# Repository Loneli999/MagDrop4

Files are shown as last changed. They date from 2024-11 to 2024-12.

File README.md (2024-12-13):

# MagDrop4
MagDrop4 is an interactive Connect4-playing machine designed to compete against a human player in real-time. The machine uses a custom-built linear belt actuator with an electromagnet to pick up magnetic game pieces from a magazine, move to the chosen column, and release each piece with accuracy. Sensors at each column track the human player's moves, allowing MagDrop4 to respond strategically, adapting its decisions based on the game’s progression. MagDrop4 showcases embedded system principles, combining real-time sensor feedback, mechanical actuation, and game strategy for an engaging human-machine interaction.

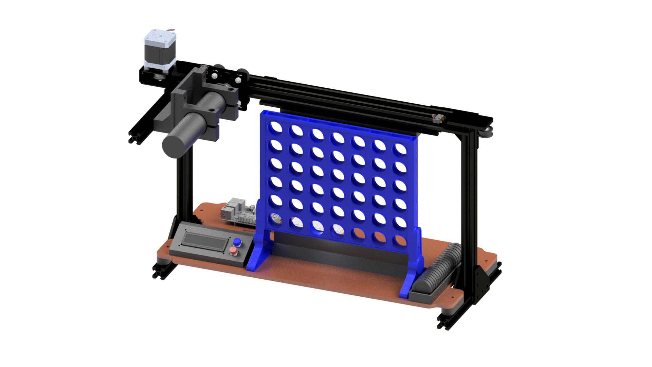
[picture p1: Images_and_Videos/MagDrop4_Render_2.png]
MagDrop4


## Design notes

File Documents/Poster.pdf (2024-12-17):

MagDrop4 | EECS 149/249A - 2018
| Leon Greiner, Murtaza Yar Hiraj, Giorgiana Rosas, Ashvin Verma
Projective Goal MagDrop4 is a real-time, interactive Connect4-playing machine designed to compete against a human on a physical Connect4 board. It uses IR sensors to detect human moves, a game AI to calculate optimal responses, and an electromagnet with magnetic game pieces for precise handling and placement. A custom belt driven linear actuator, powered by a stepper motor, ensures accurate piece placement. This project showcases advanced sensor integration, motor control, and AI-driven | | Game Engine The game engine uses a Minimax algorithm enhanced with Alpha-Beta Pruning to optimize the AI's moves efficiently. A heuristic evaluates board states by scoring windows with 4, 3, and 2 AI pieces as (+100, +10, +5), penalizing opponent windows as (-100, -8, 0), and prioritizing central play.

decision-making in a dynamic autonomous system.

## Mechanical Design

The main structure is built from standard aluminum profiles, which also serve as the guide rail for the gantry cart of the linear actuator. The baseplate is precision laser-cut from plywood. Numerous components, including mountings, the magazine, and game discs, are 3D-printed using PLA. The magazine uses a spring mechanism to continuously push the game discs toward the grabbing point..

## System Integration and Results

The final system delivers real-time interaction, accurate gameplay execution, and competitive AI performance, showcasing the success of combining precision mechanics, sensor integration, and advanced algorithms. The gantry cart completes its cycle in <5 secs: detecting human play, computing the AI’s move, placing a piece, and resetting for the next turn. This highlights the system’s speed and seamless integration.

2024

## Machine Logic

The system uses a Finite State Machine (FSM) to manage gameplay flow: It detects human moves via IR
sensors, calculates the AI’s optimal move using the game
engine, and precisely places pieces with the belt driven
linear actuator. | Electrical Design
| The electrical system is built around a Raspberry Pi 3+,
| handling motor control, sensor inputs, and display output. Power is supplied via 5V and 16V lines, with an I2C interface
| managing the display and the stepper motor controlled by a
| DRV8825 motor driver, connected via an extension board to
| the Raspberry. Furthermore, we use an N-channel logic-level
| MOSFET to control the 16V electromagnet via a GPIO pin.

Simplified illustration of the Systems FSM

Disc Magazine

Gantry Cart with
Electromagnet

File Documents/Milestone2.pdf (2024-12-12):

# Project Title: MagDrop4

Team: Leon Greiner, Murtaza Yar Hiraj, Giorgiana Rosas, Ashvin Verma

EECS 149/249A Milestone 2, Fall 2024

## Project Goal

The goal of MagDrop4 is to create an engaging and competitive Connect4-playing machine that can seam-lessly interact with a human player in real-time. By integrating advanced embedded systems, mechanical precision, and strategic gameplay, MagDrop4 aims to demonstrate the capabilities of autonomous systems in responsive, interactive applications. The project also serves as a practical exploration of sensor integration, motor control, and real-time decision-making within an embedded system framework.

## Progress

Mechanical Design

We have completed printing all the 3D parts and assembling the mechanical structure of the machine. The mechanical structure mainly consists out of normed aluminum profiles, which can be easily assembled. The final step remaining is to create the baseplate. We are currently deciding whether to laser-cut the plate or manually cut and drill it from plywood, depending on the availability of a laser cutter.

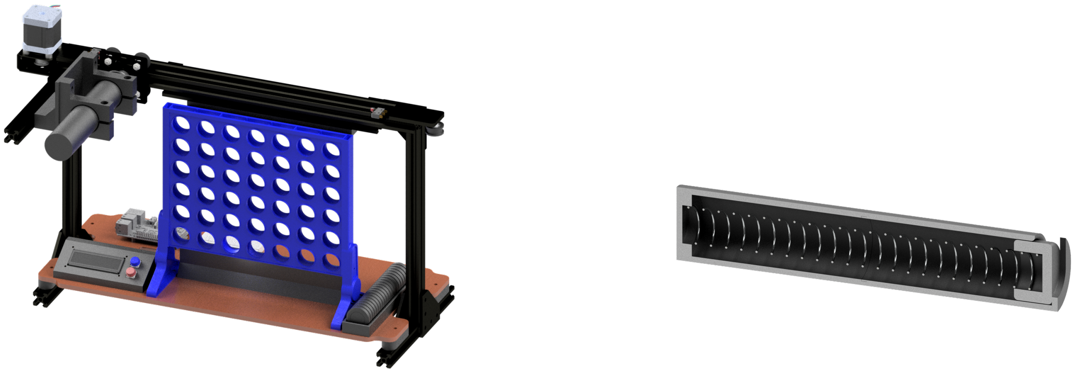
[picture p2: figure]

Figure 1: CAD Rendering of MagDrop4

Figure 2: CAD Rendering of the Game Piece Magazine

Electrical Design

The electrical design includes the complete circuitry, with the Raspberry Pi serving as the central control unit. The display is managed via an SPI interface, utilizing GPIO pins 10, 9, 8, and 7. A stepper motor is driven by the DRV8829 driver, conveniently connected through a extension shield. The motor control uses GPIO 11 for direction, GPIO 12 (PWM) for step control, and GPIO 13 for enable. The Motor gets powered by a 24V. For the human move detection, seven IR sensors are powered by 5V. These sensors provide a simple high/low signal depending on whether a move is detected, and they are connected to GPIO pins 0 through 6. Each sensor’s sensitivity can be adjusted individually using a sensitivity screw on the sensor. Two limit switches are used to mark the farthest left and right positions of the gantry cart on the linear rail. These are configured in a Normally Open (NO) setup, connected to GPIO pins 14 and 15. Each switch is connected to 3.3V through a pull-up resistor. Similarly, two additional buttons for user input are connected to GPIO pins 16 and 17 in the same NO configuration.

FSM and Machine Logic

The following FSM diagram illustrates the complete logic of the machine, starting from the initial setup to the conclusion of the game, either when there is a winner or the game ends in a draw. At the beginning, the machine moves the gantry cart away from the magazine, so there is more room to reload the magazine with the game pieces. Then the machine prompts the user to confirm if the magazine is fully loaded with game pieces and whether the game can proceed. Before starting, the user is also given the opportunity to adjust the AI’s difficulty level. During Human Turn, the system checks if the IR sensor for a specific column is triggered and after that the machine waits for up to 2 seconds for a valid new IR trigger. This allows for situations where the human player initially places a piece in one column, but then decides to retrieve it and drop it into another. The Game Engine, which handles the rules and logic for determining the next moves and checking for game completion, will be detailed in a separate section. The AI Turn controls the movement of the gantry cart to the desired column and manages the activation and deactivation of the electromagnet to place the game piece accurately.

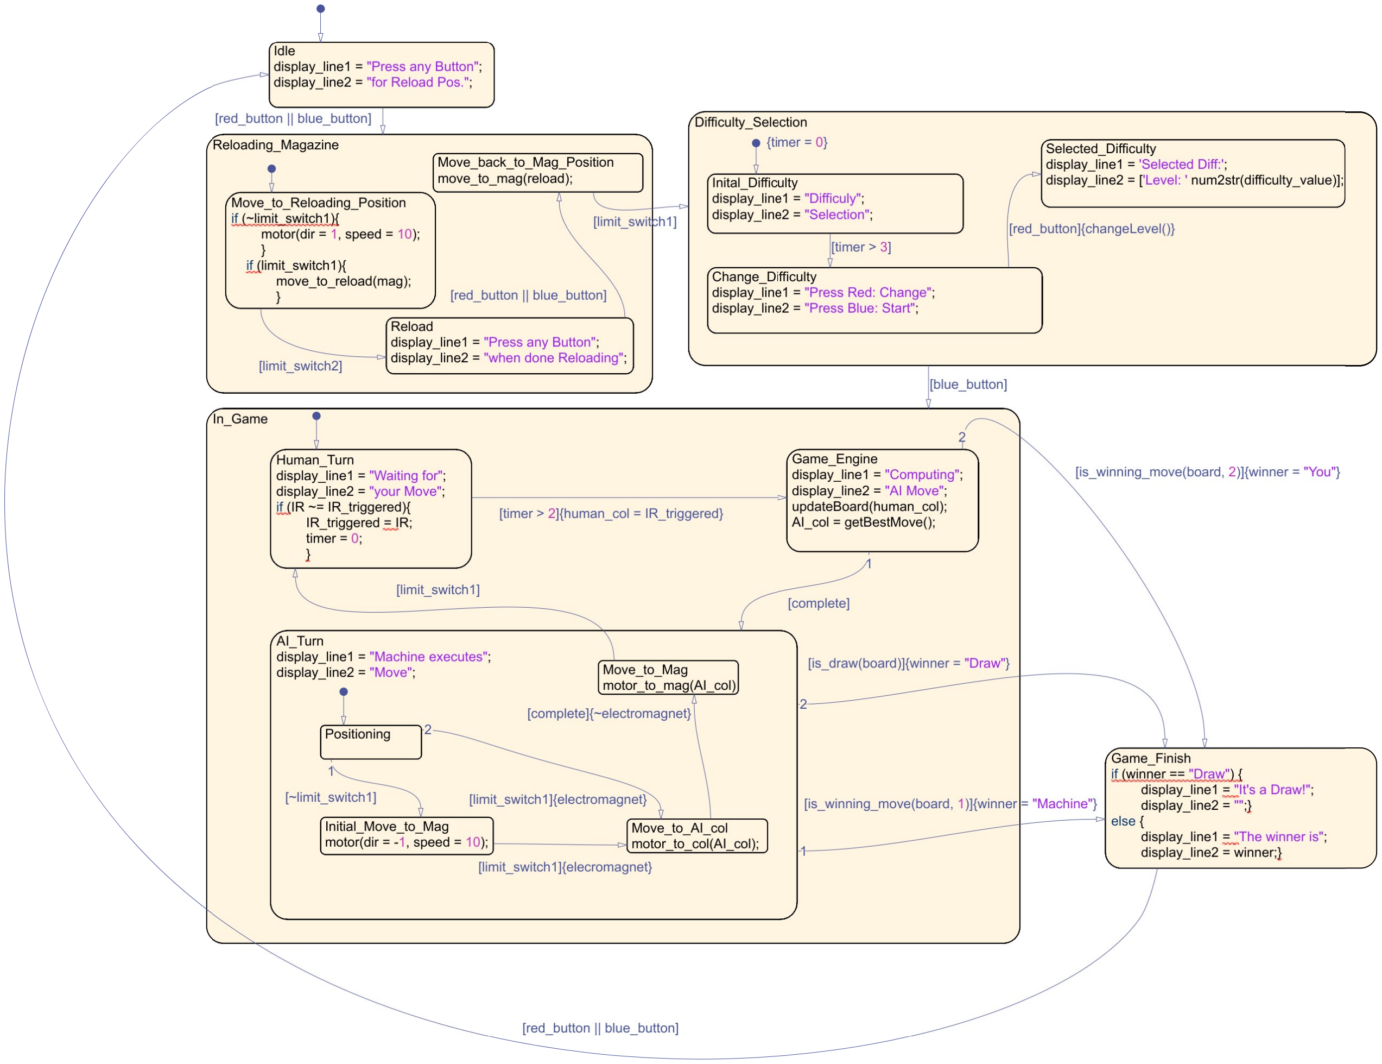
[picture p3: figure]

Figure 3: Finite State Machine of MagDrop4

Game Engine

We successfully developed a functional game engine prototype, which computes the computer’s move in maximum 30 ms (depth = 4) on a standard laptop. This suggests it should operate within acceptable time limits on the Raspberry Pi 3+. The game engine utilizes a Minimax Search algorithm with Alpha-Beta Pruning, allowing us to implement different difficulty levels by adjusting the search depth (ranging from 1 to 4).
Minimax is a tree search algorithm that evaluates all possible moves by both the human and the computer up to a specified depth. At the terminal nodes of the tree, a scoring function determines the relative value of the board position. The scoring system is critical for the game engine’s effectiveness. We have chosen the following scoring parameters, which can be fine-tuned as needed:
- AI’s 3-in-a-Row with 1 Empty Space: score + = 10
- AI’s 2-in-a-Row with 2 Empty Spaces: score + = 5
- Human 3-in-a-Row with 1 Empty Space: score − = 15
- Terminal State (AI Wins): score + = 100, 000
- Terminal State (Human Wins): score − = 100, 000

We also included Alpha-Beta Pruning, which enhances computational efficiency by eliminating branches in the search tree that cannot influence the final outcome. This significantly reduces the number of paths evaluated and speeds up decision-making. At a search depth of 4, the AI is already challenging to beat and sufficient for our purposes. Increasing the depth to 6 makes it basically impossible for a human to win against the machine. However, the computational cost increases exponentially, potentially exceeding the capabilities of the Raspberry Pi 3+. Further testing is required to determine the feasibility of deeper searches on the hardware.

## Resources

Name | Quantity | Name | Quantity
400-Point Breadboard | 1 | M3 Screw | 17
Aluminum Spacer | 4 | M5 Nut | 25
Belt Clamp | 2 | M5 Screw | 100
Connect 4 Game Set | 1 | M5 T-Nut | 1
Corner Connector 2020 | 1 | Metal Disk Inserts | 42
Display | 1 | Limit Switch Plate | 2
DRV8825 Extension Board | 1 | Mosfet | 1
Electromagnet | 1 | Raspberry Pi 3 Model B+ | 1
Gantry Cart | 1 | Round Switch | 2
GT2 Belt | 1 | Spring | 1
Idler Pulley | 1 | Stepper Motor | 1
Idler Pulley Plate | 1 | Stepper Motor Driver (DRV8825) | 1
IR Sensor | 7 | Superglue | 1
L-Connector | 7 | Timing Pulley | 1
Limit Switch | 2 | USB 2.0 A to Micro B cable | 1
M2.5 Screw | 4 | USB Power Supply | 1
M3 Insert x 5mm | 7 | V-Slot 20x20 100mm | 4
V-Slot 20x20 200mm | 1 | V-Slot 20x20 300mm | 3
V-Slot 20x40 500mm | 1 | V-Slot Cover | 2
V-Slot Endcap | 2
3D Printed Parts
Base Plate Spacer | 4 | Disk Holder | 1
Control Mount | 1 | Idler Pulley Overlay | 1
Disk | 42 | IR Mount Plate | 1
Disk Barrier | 1 | Raspberry Pi Standoff | 4
Spring Top | 1 | Base Plate (Laser Cut) | 1

Table 1: Purchase and Checkoff Parts List with Additional 3D Printed Parts

## Timeline

- 12.10. - Completion of Wiring: All electrical components, including sensors, motors, and actuators, are fully wired and tested for connectivity.
- 12.14. - Code Implementation Finalized: Core logic for gameplay, motor control, and sensor integration are implemented.
- 12.16. - Bug Fixing and Full Machine Operation: Final debugging and calibration completed. The machine is fully functional and ready for demonstration.

## GitHub Repo

https://github.com/Loneli999/MagDrop4.git

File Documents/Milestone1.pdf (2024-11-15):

# Project Title: MagDrop4

Team: Leon Greiner, Murtaza Yar Hiraj, Giorgiana Rosas, Ashvin Verma

EECS 149/249A Milestone 1, Fall 2024

## Project Goal

The goal of MagDrop4 is to create an engaging and competitive Connect4-playing machine that can seamlessly interact with a human player in real-time. By integrating advanced embedded systems, mechanical precision, and strategic gameplay, MagDrop4 aims to demonstrate the capabilities of autonomous systems in responsive, interactive applications. The project also serves as a practical exploration of sensor integration, motor control, and real-time decision-making within an embedded system framework.

## Project Approach

To achieve this, MagDrop4 combines a custom-built linear belt actuator, powered by a stepper motor, with an electromagnet end effector that precisely handles and places the custom-made 3D printed game disks with steel inserts. A set of IR sensors at each column allows the machine to monitor and react to the human player’s moves, updating its strategy based on the evolving game state. The system is powered by a Raspberry Pi, which manages the game logic, motor control, and sensor input, creating a dynamic response to each move.

## Progress

We’ve developed a first prototype of MagDrop4 in CAD (see Figure 1). We successfully designed a beltdriven system powered by a single stepper motor. This stepper motor with a step size of 0.9°, combined with two limit switches positioned at the ends of the rail, ensures precise movement of the sledge. While this prototype is a great initial step, several improvements are planned. We need to redesign the magazine to increase its capacity, allowing for more game pieces to be stored and deployed. Additionally, we still need to implement the mounting for the linear sled, as it currently hovers without a fixed support structure.

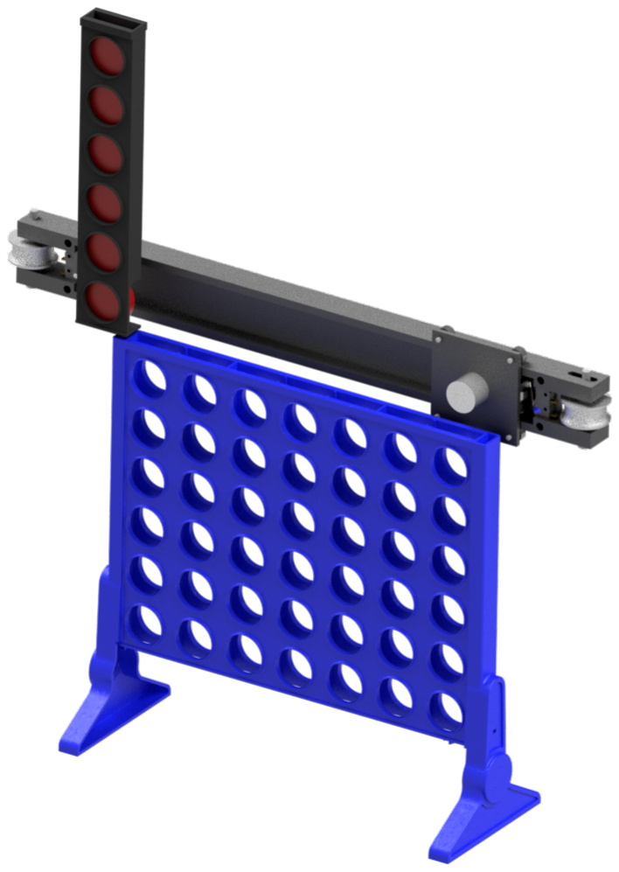
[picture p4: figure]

Figure 1: Rendering of the first prototype

1

## Resources

All the essential parts for MagDrop4 are listed in the table, showing both items we’re purchasing and those we already have on hand, each with its corresponding price and checkoff number. We’ve slightly exceeded the $100 budget, but this covers all important components, including a Raspberry Pi, a stepper motor, power supplies, and bearings.
Our custom frame components, including the rail, sled, and mounting structures will be 3D printed. This approach gives us flexibility in the design process and is virtually free, since we can use the 3D printers in Cory Supernode and pay for the filament we use. Besides these listed items, only minor additions like wires or washers may be needed as we assemble the system.
Name | Qty | Checkoff # | Price | Link
Raspberry Pi 3 Model B+ | 1 | 13 | - | Link (https://www.raspberrypi.com/products/raspberry-pi-3-model-b-plus/)
Electromagnet | 1 | 245 | - | Link (https://www.amazon.com/uxcell-Electric-Lifting-Electromagnet-Solenoid/dp/B01N3387AA)
Limit Switch | 2 | 145 | - | Link (https://www.amazon.com/InduSKY-Switch-Momentary-Roller-Switches/dp/B08736NP44)
IR Receiver & Transmitter | 7 | 265 | - | Link (https://www.amazon.com/Digital-Receiver-Transmitter-Electronic-Building/dp/B08X2MFS6S)
Stepper Motor | 1 | 213 | - | Link (https://www.ebay.com/itm/154024578430)
On-Off Toggle Switch | 1 | 141 | - | Link (https://www.amazon.com/Position-Automobile-Appliance-Industrial-Control/dp/B07XB2JC14)
USB Power Supply | 1 | 301 | - | Link (https://thereviewindex.com/us/p/Wall_Charger_UROPHYLLA_3_Pack_5V_2_4A_Mini_Universal_Portable_Home_Travel_Adapter_USB_Wall_Charger_f/AZ-US_B06X9PY6RT)
USB 2.0 A to Micro B cable | 1 | 318 | - | Link (https://thereviewindex.com/us/p/Wall_Charger_UROPHYLLA_3_Pack_5V_2_4A_Mini_Universal_Portable_Home_Travel_Adapter_USB_Wall_Charger_f/AZ-US_B06X9PY6RT)
Connect 4 Game Set | 1 | - | $ 9.99 | Link (https://www.amazon.com/Hasbro-A5640-Connect-4-Game/dp/B00D8STBHY)
Sledge Bearing (BS69310-5) | 6 | - | $ 10.20 | Link (https://www.aliexpress.us/item/1005003690085583.html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)
Stepper Motor Driver (DRV8825) | 1 | - | $ 8.99 | Link (https://www.amazon.com/DiGiYes-DRV8825-Stepper-Driver-Printer/dp/B0BXL5VYPT)
DRV8825 Extension Board | 1 | - | $ 7.99 | Link (https://www.amazon.com/Ximimark-DRV8825-Printer-Stepper-Extension/dp/B07L74WZPS)
Power Supply 24V | 1 | - | $ 19.99 | Link (https://www.amazon.com/EMITEVER-Lighting-Transformers-100-240V-UL-Listed/dp/B095VWHPCC?s=hi)
Timing Pulley with Teeth (2GT-40T 11 5) | 1 | - | $ 5.35 | Link (https://www.ebay.com/itm/156393844989?_skw=2gt+40t&itmmeta=01JC6F1FEDNC6WNQF3JPT0Q8V1&var=457485017278)
Timing Pulley without Teeth (2GT-40T 11 5) | 1 | - | $ 5.35 | Link (https://www.ebay.com/itm/226059144256)
2GT Timing Belt | 1 | - | $ 2.95 | Link (https://www.ebay.com/itm/256243562695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)
Steel Disk Inserts | 1 | - | $ 19.99 | Link (https://www.amazon.com/totalElement-Steel-Discs-Strike-Plates/dp/B09BXWJ772?sp_csd=d2lkZ2V0TmFtZT1zcF9hdGY)
Various Screws, Nuts and Washers | 1 | - | ≈ $ 30 | Link (https://www.ebay.com/itm/256243562695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)
Total | | | $120.81

Table 1: Purchase and Checkoff Part List

## Major Risks

Major risks include challenges in constructing and testing the custom linear actuator, ensuring smooth integration of hardware and software components, and maintaining real-time response accuracy to enable interactive gameplay. Additionally, reliance on 3D-printed parts introduces potential delays or issues with part quality, which could impact system precision and reliability.

## Timeline & Responsibilities

- November 18: Murtaz and Giorgiana finish the game software model
- November 21: Leon and Ashvin finalize actuator assembly and testing.
- November 28: Finish hardware and software integration
- December 8: Work on final demo and integration

## GitHub Repo

https://github.com/Loneli999/MagDrop4.git

2

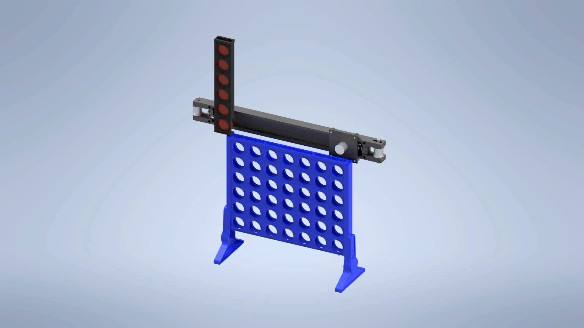
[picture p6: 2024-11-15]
Images_and_Videos/Render_Animation_Prototype_1.gif

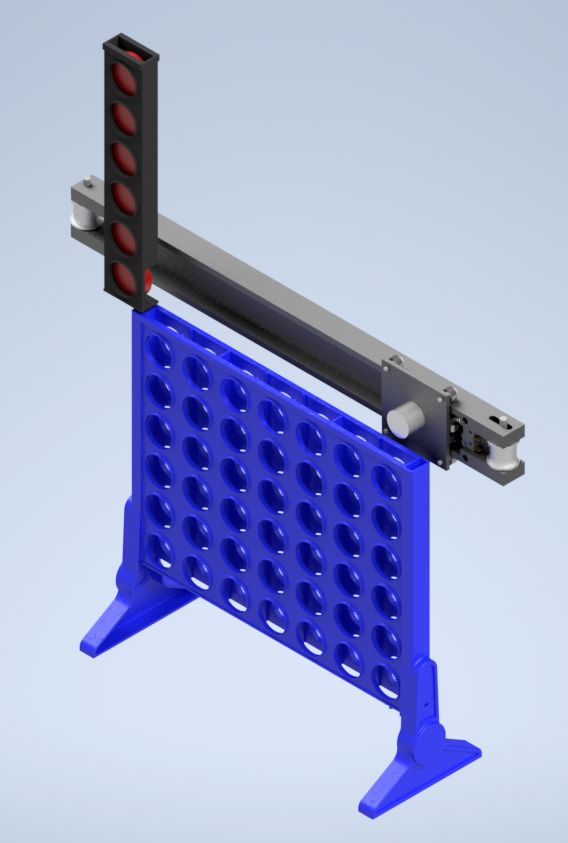
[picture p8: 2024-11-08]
Images_and_Videos/Render_Prototype_1_cropped.png

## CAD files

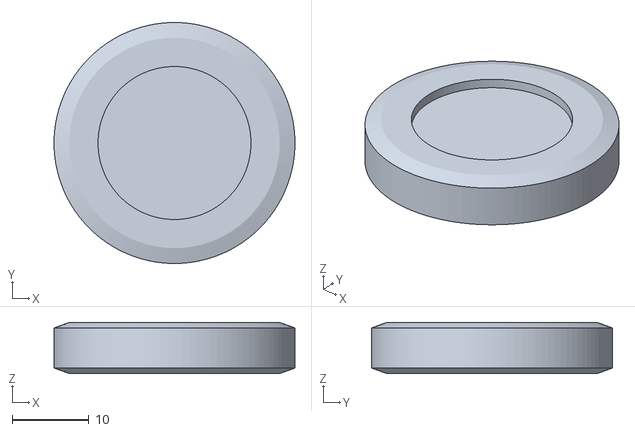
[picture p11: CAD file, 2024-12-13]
CAD_Model/3DPrint_Parts/3DPrint_Files/Disk_machine.stl
31.5 x 31.5 x 6.70

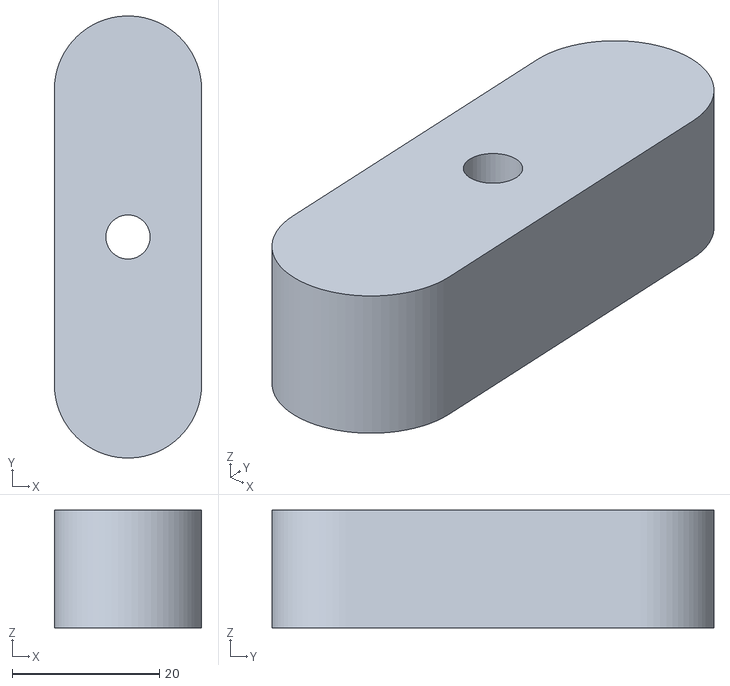
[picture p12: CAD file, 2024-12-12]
CAD_Model/3DPrint_Parts/3DPrint_Files/Base_Plate_Spacer.stl
20.0 x 60.0 x 16.0

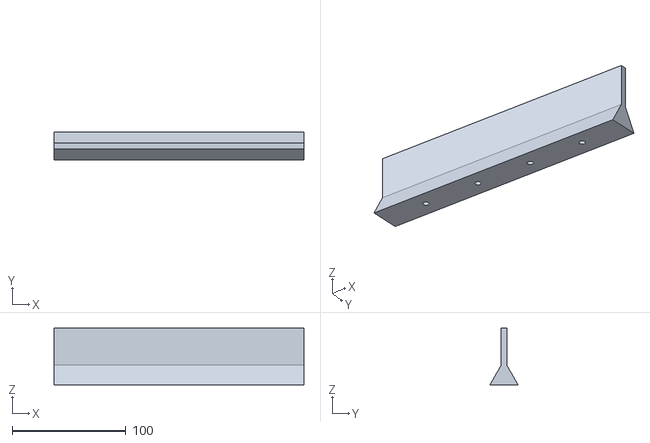
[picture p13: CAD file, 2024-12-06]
CAD_Model/3DPrint_Parts/3DPrint_Files/Disk_Barrier.stl
220.0 x 25.0 x 50.0

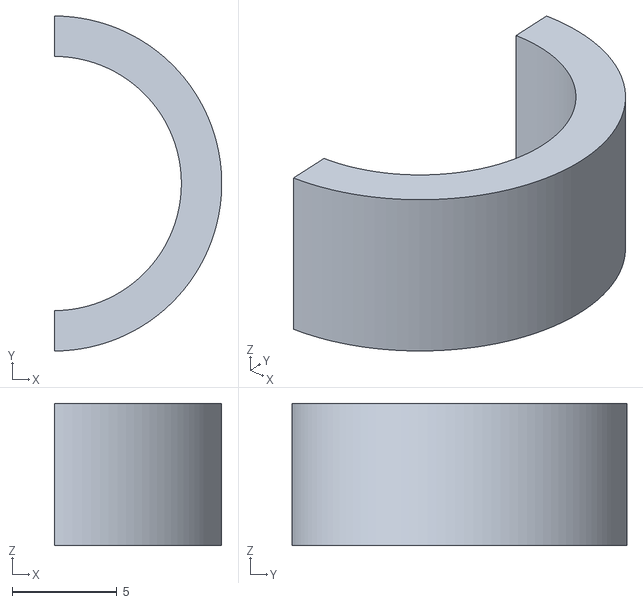
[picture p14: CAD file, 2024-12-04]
CAD_Model/3DPrint_Parts/3DPrint_Files/Idler_Pulley_Insert.stl
8.00 x 16.0 x 6.80

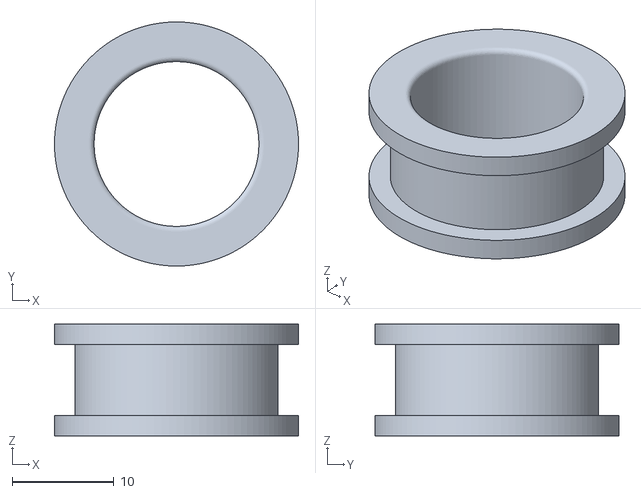
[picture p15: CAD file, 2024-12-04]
CAD_Model/3DPrint_Parts/3DPrint_Files/Idler_Pulley_Overlay.stl
24.0 x 24.0 x 11.0

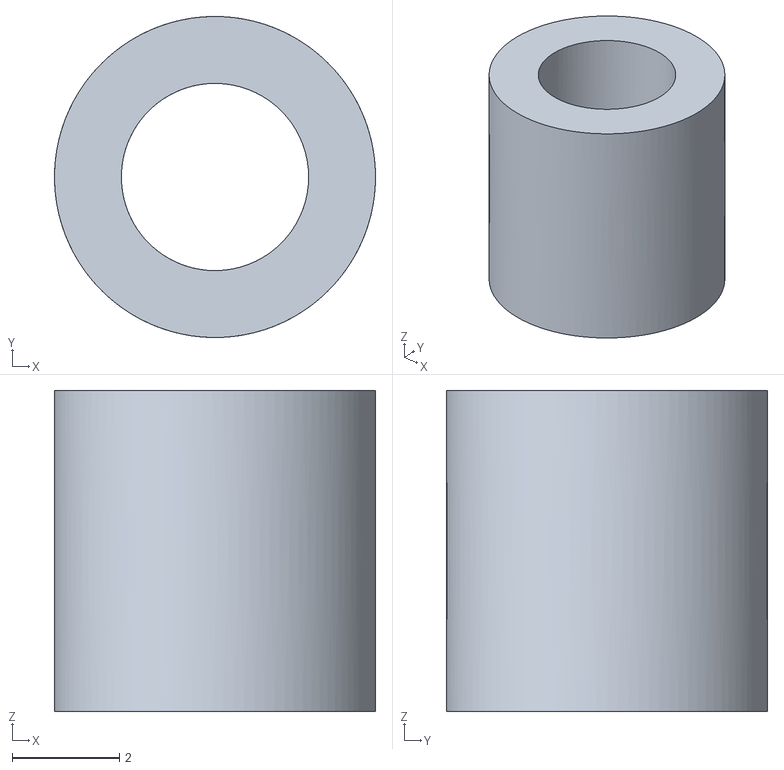
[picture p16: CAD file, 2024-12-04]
CAD_Model/3DPrint_Parts/3DPrint_Files/Raspberry_Pi3_Standoff.stl
6.00 x 6.00 x 6.00

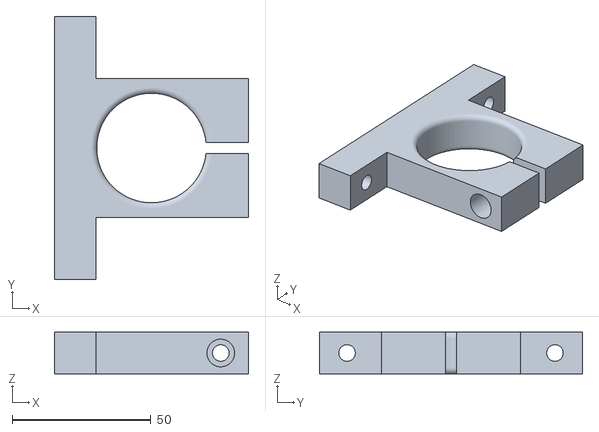
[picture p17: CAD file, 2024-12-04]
CAD_Model/3DPrint_Parts/3DPrint_Files/Magazine_Holder.stl
70.0 x 95.0 x 15.0

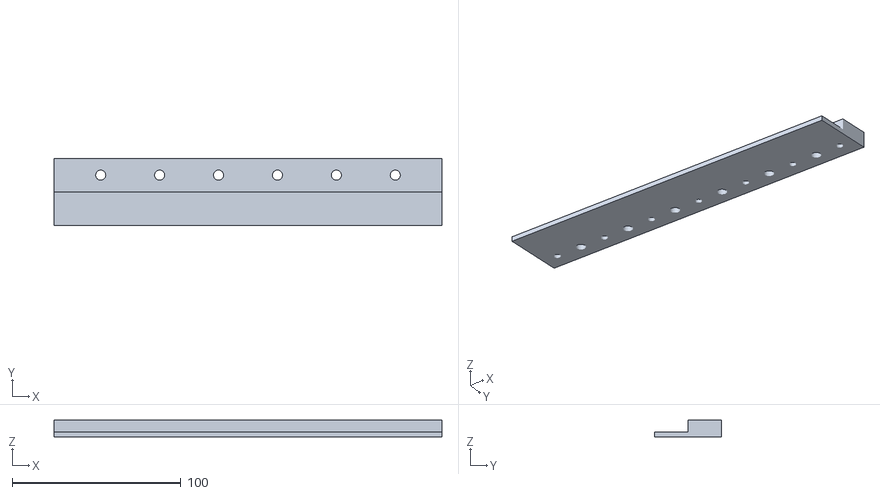
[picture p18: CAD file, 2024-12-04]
CAD_Model/3DPrint_Parts/3DPrint_Files/IR_Mount_Plate.stl
230.0 x 40.0 x 10.0

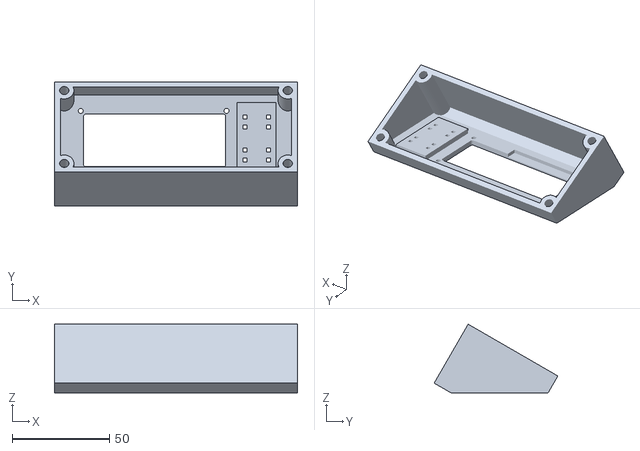
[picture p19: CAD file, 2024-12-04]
CAD_Model/3DPrint_Parts/3DPrint_Files/Control_Mount.stl
125.0 x 63.7 x 35.3

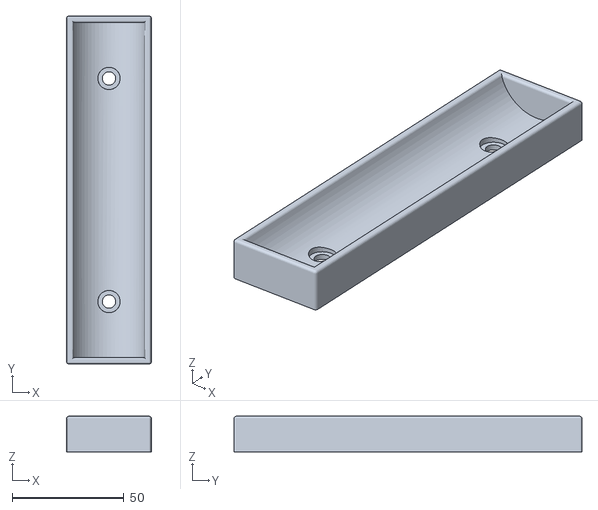
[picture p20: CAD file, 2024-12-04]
CAD_Model/3DPrint_Parts/3DPrint_Files/Disk_Holder.stl
38.0 x 156.0 x 16.0

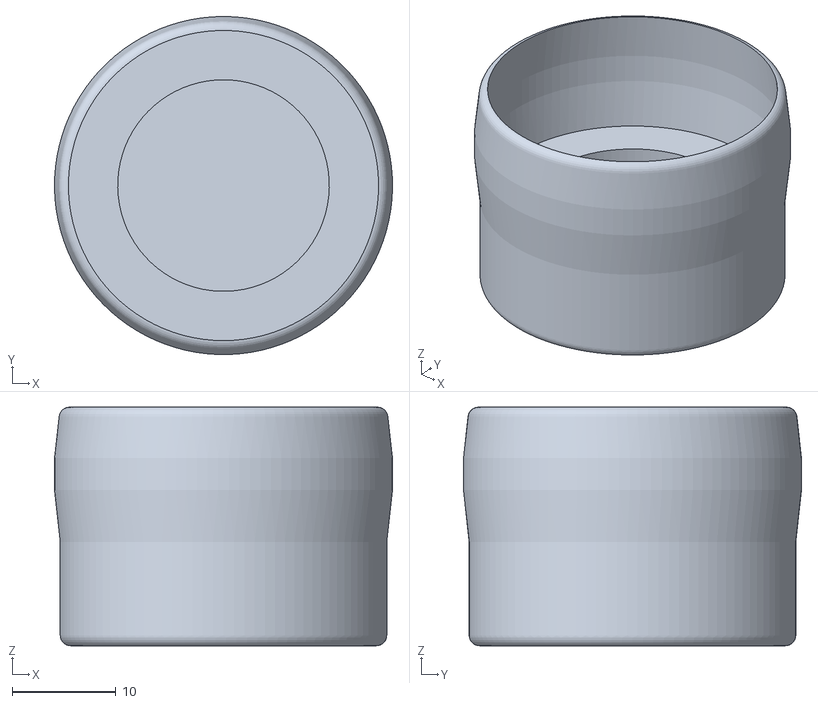
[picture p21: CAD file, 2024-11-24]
CAD_Model/3DPrint_Parts/3DPrint_Files/Spring_Top_2.stl
32.6 x 32.6 x 23.0

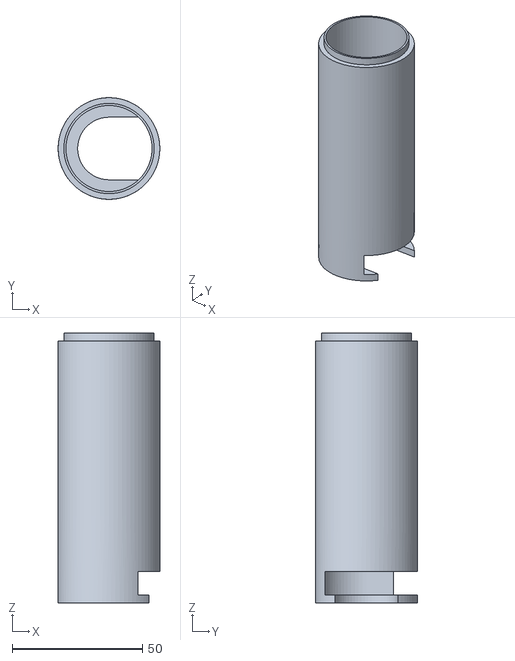
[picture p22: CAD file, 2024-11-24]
CAD_Model/3DPrint_Parts/3DPrint_Files/Magazine_Tube_2.stl
39.0 x 39.0 x 103.5

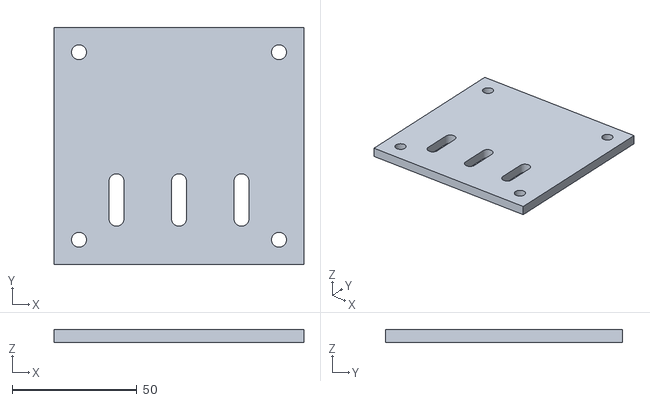
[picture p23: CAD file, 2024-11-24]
CAD_Model/3DPrint_Parts/3DPrint_Files/Magazine_Mount_Plate.stl
100.0 x 95.0 x 5.00

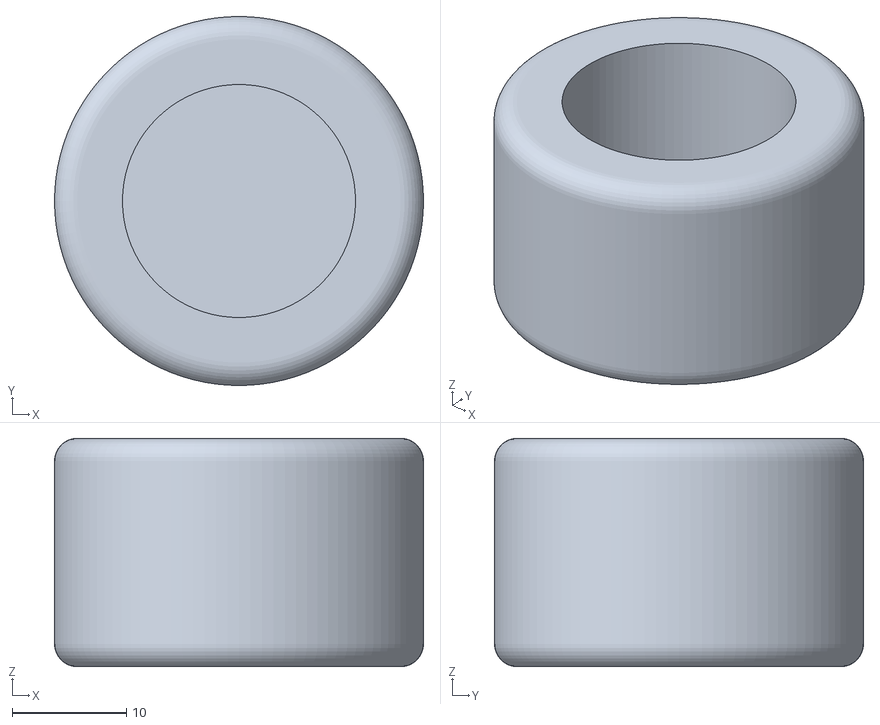
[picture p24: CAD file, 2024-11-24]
CAD_Model/3DPrint_Parts/3DPrint_Files/Spring_Top.stl
32.3 x 32.3 x 20.0

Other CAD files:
CAD_Model/3DPrint_Parts/3DPrint_Files/Magazine_Mount_Plate_Spacer.stl
CAD_Model/3DPrint_Parts/3DPrint_Files/Disk.stl
CAD_Model/3DPrint_Parts/3DPrint_Files/Base_Plate.stl
CAD_Model/3DPrint_Parts/3DPrint_Files/Magazine_Tube_1.stl
CAD_Model/3DPrint_Parts/3DPrint_Files/Spring_Top_1.stl
CAD_Model/3DPrint_Parts/Base_Plate_Spacer.ipt
CAD_Model/3DPrint_Parts/Control_Mount.ipt
CAD_Model/3DPrint_Parts/Disk.ipt
CAD_Model/3DPrint_Parts/Disk_Barrier.ipt
CAD_Model/3DPrint_Parts/Disk_Holder.ipt
CAD_Model/3DPrint_Parts/Disk_machine.ipt
CAD_Model/3DPrint_Parts/IR_Mount_Plate.ipt
CAD_Model/3DPrint_Parts/IR_Mount_Plate_1.ipt
CAD_Model/3DPrint_Parts/IR_Mount_Plate_2.ipt
CAD_Model/3DPrint_Parts/Idler_Pulley_Insert.ipt
CAD_Model/3DPrint_Parts/Idler_Pulley_Overlay.ipt
CAD_Model/3DPrint_Parts/Magazine_Holder.ipt
CAD_Model/3DPrint_Parts/Magazine_Mount_Plate.ipt
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

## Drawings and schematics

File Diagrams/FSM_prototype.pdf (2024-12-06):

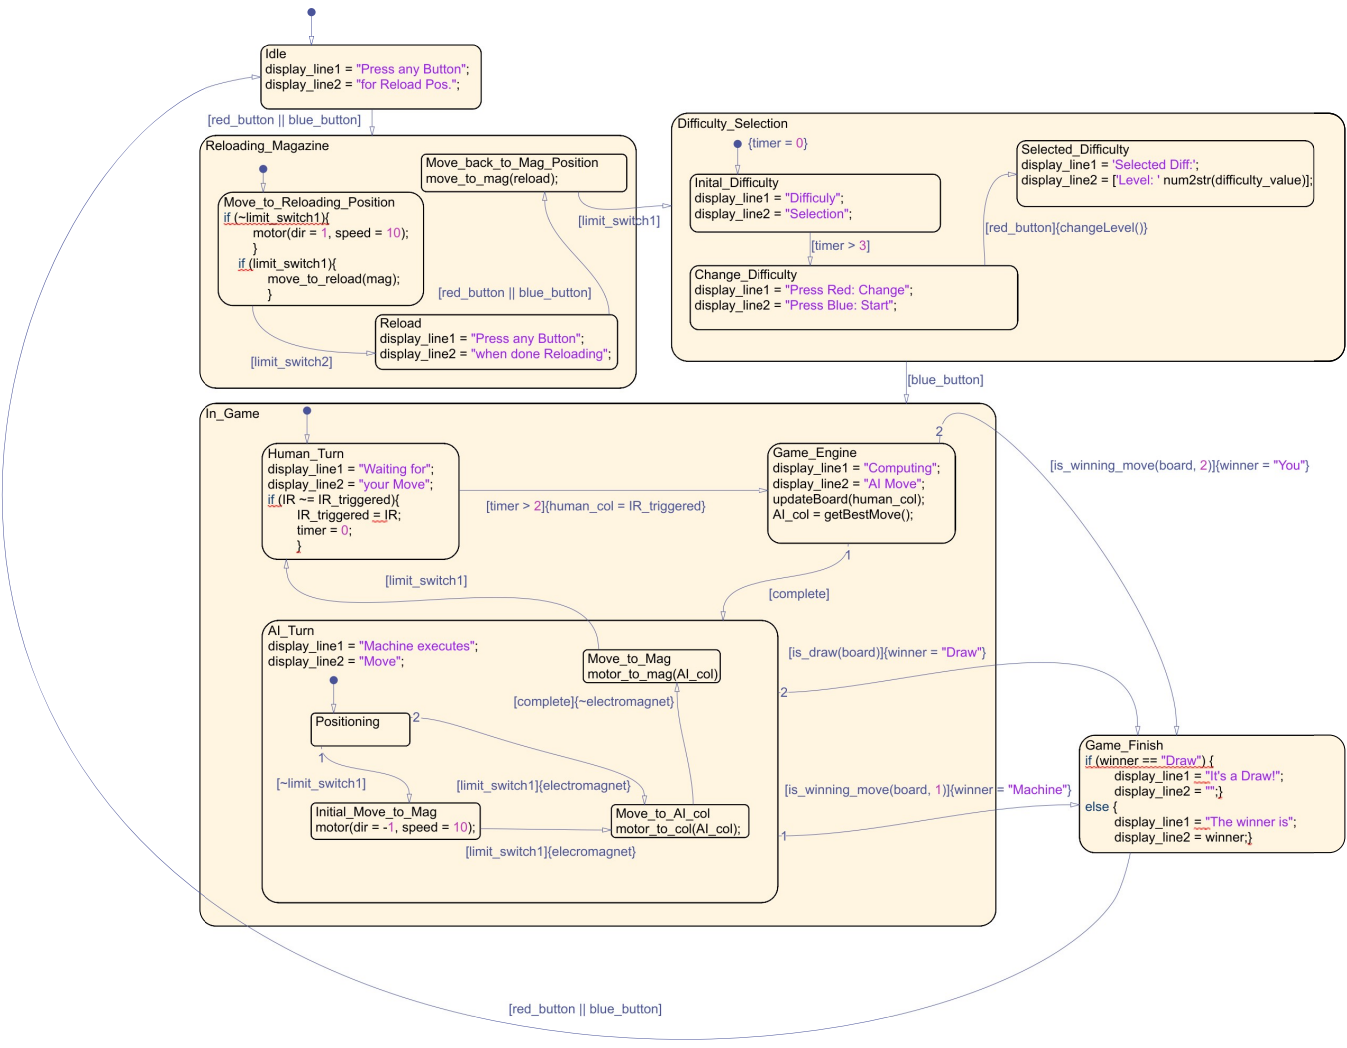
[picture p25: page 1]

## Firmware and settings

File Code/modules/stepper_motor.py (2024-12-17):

import RPi.GPIO as GPIO
import time
from modules.limit_switch_reader import read_limit_switches

# GPIO pin configuration
STEP_PIN = 16       # Step control
DIR_PIN = 21        # Direction control
ENABLE_PIN = 20     # Enable motor

DELAY = 0.0001  # Delay between steps

# GPIO setup
GPIO.setmode(GPIO.BCM)
GPIO.setup(STEP_PIN, GPIO.OUT)
GPIO.setup(DIR_PIN, GPIO.OUT)
GPIO.setup(ENABLE_PIN, GPIO.OUT)

def motor_off():
    GPIO.output(ENABLE_PIN, GPIO.HIGH)

def move_motor(direction, steps):
    GPIO.output(ENABLE_PIN, GPIO.LOW)  # Enable the motor driver

    # Set direction
    if direction == 'left':
        GPIO.output(DIR_PIN, GPIO.HIGH)
    elif direction == 'right':
        GPIO.output(DIR_PIN, GPIO.LOW)
    else:
        print("Invalid direction! Use 'left' or 'right'.")
        return

    # Step the motor
    for step in range(steps):
        # Check limit switches
        left_switch, right_switch = read_limit_switches()
        if direction == 'left' and left_switch:
            break
        elif direction == 'right' and right_switch:
            break

        # Generate step pulse
        GPIO.output(STEP_PIN, GPIO.HIGH)
        time.sleep(DELAY)
        GPIO.output(STEP_PIN, GPIO.LOW)
        time.sleep(DELAY)

    GPIO.output(ENABLE_PIN, GPIO.HIGH)  # Disable the motor driver

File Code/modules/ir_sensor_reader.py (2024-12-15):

import RPi.GPIO as GPIO

# IR sensor pins
IR_PINS = [26, 17, 27, 22, 23, 24, 4]

# GPIO setup
GPIO.setmode(GPIO.BCM)
for pin in IR_PINS:
    GPIO.setup(pin, GPIO.IN, pull_up_down=GPIO.PUD_UP)

def read_ir_sensors(ignore_sensors=[]):
    triggered_sensors = []

    for index, pin in enumerate(IR_PINS):
        sensor_number = index + 1
        if sensor_number in ignore_sensors:
            continue  # Skip ignored sensors

        if GPIO.input(pin) == GPIO.LOW:
            triggered_sensors.append(index + 1)

    if len(triggered_sensors) == 1:
        return triggered_sensors[0]  # Return the single triggered sensor number
    else:
        return None  # No sensors or more than one sensor triggered

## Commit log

2024-11-08 Added CAD_Model and Images+Videos
    [Assembly.0007.iam, Assembly.iam, BOM_View_Prototype_1.idw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]
2024-11-15 Edited CAD_Model
    [Alu_Spacer.ipt, Aluminum Spacer 6mm v1.ipt, Assembly.0007.iam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]
2024-11-16 Edited CAD Model
    [Base_Plate.0009.ipt, Base_Plate.0010.ipt, Base_Plate.ipt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]
2024-11-16 Add Game Engine Prototype
    [IR_Mount_Plate.0007.ipt, IR_Mount_Plate.0008.ipt, IR_Mount_Plate.ipt]
2024-11-27 abstracting away game board
